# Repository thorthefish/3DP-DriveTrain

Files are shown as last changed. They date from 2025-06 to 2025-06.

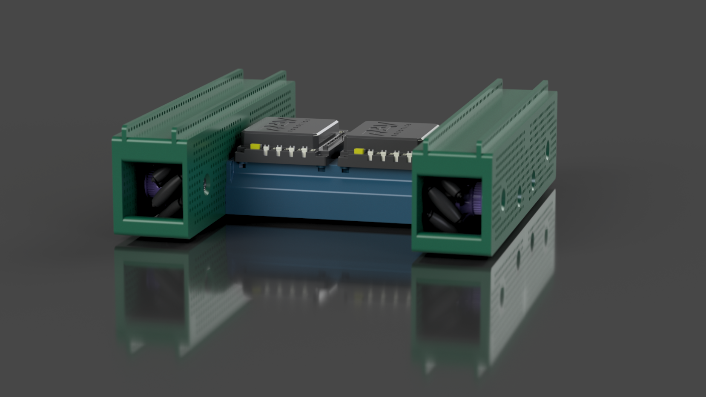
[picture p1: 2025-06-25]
Pictures/render_1.png

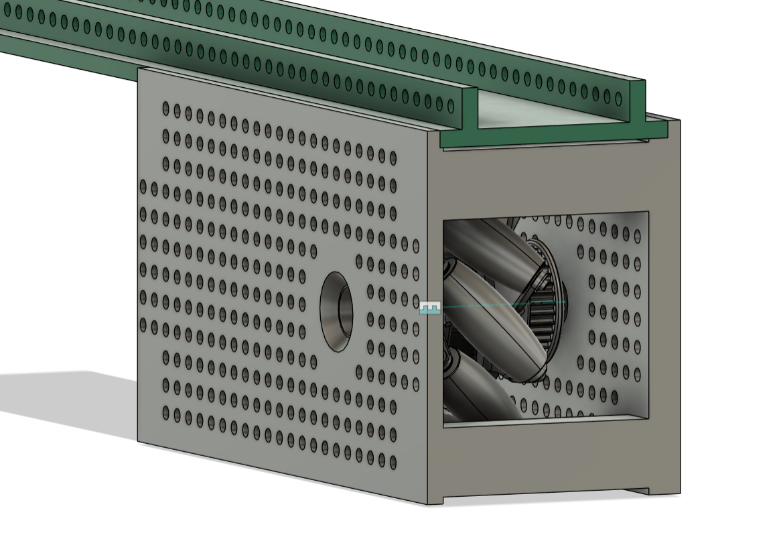
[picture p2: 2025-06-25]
Pictures/Fusion360_dO0HVU8Hnw.png

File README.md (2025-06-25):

# 3D Printed FTC Drivetrain
A Fully 3D Printed FTC Drivetrain

----

render_1

# WHY???

The reason behind this project is my dream for a good, customisable, and strong drivetrain. Whenever it is brought up, it usualy leads to immidiate dismissal, so this is to prove to all teams that a 3D Printed chassis is a good choice for a chassis. This proves that 3D printing is strong enough to compete with aluminum, light enough to compete with carbon fiber, and more versitle than either.

# What

This is A drivetrain using 3d printed parts wherever possible. It is compatable with the gobilda architecture for connecting to most of their standard products (eg. viper slides)

- It can be easily adjusted to almost sny situation, and is incredibly easy to add parts and modules to. 
- works in 3 dimensions, unlike traditional parallel plate designs
- Easy to design around, This is not limited to a single season, it can be addaped to almost any game with a few hours of CAD.
- Mounting, Top rails for any modules immaginable, grids on wass for anything form team markers, odo pods, to linear slides
- Incredibly light, uses around 1kg of filament for an entire chassis

# CAD

Fusion360_uBIizt1Rju

Fusion360_99nrl9oc8i

Fusion360_UiN48u3bqZ

#FEA(AKA. Finite Element Analisis (AKA. Find Weak Points))

This was the most improtant part of this project, it provided the evidence I needed to show that this was a viable option.
The incredible rigidity of PLA is acctualy crucial to this, as other filaments would deform under lesser pressures, so it is the ideal material in this case.

Fusion360_l8kNUF9FA9

Fusion360_3vuXtYZTeW

----
# Assembly

You need to print two instances of the DT_Wheel_Hub files each, they each go on opposite corners, the two files are mirrored copies of the other. Print one instance of the brace, and attach it with 15 mm M4 bolts, the bottoms should be flush and it should go in the direct middle. Refer to cad if needed. The bolts do not need to be in a specific location, just try to get at least 8 points of contact per side.

----
# BOM

|3DP DT|# Needed|# to Purchase|Price /unit|Price Total|Source|
|-|-|-|-|-|-|
||||||
|To Buy| | | | | |
||||||
|Filament 2kg |1 |1 |26 |26 |https://www.amazon.com/ELEGOO-Filament-Dimensional-Accuracy-Cardboard/dp/B0BM7465PB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|
|Timing belts - HTD 3 100T |4 |4 |7 |28 |https://www.gobilda.com/3403-series-3mm-htd-pitch-timing-belt-15mm-width-300mm-pitch-length-100-tooth/ |
|Bearings - 14mm OD 8mm ID Flanged 2pc |2 |2 |4 |8 |https://www.gobilda.com/1611-series-flanged-ball-bearing-8mm-id-x-14mm-od-5mm-thickness-2-pack/ |
|Shafts - 72mm REX |4 |4 |5 |20 |https://www.gobilda.com/2106-series-stainless-steel-rex-shaft-8mm-diameter-72mm-length/ |
|REX Sonic Hubs |4 |4 |8 |32 |https://www.gobilda.com/1309-series-sonic-hub-8mm-rex-bore/ |
||||||
|Alredy Owned | | | | | |
|Hubs |2 |N/A |N/A | | |
|Battery |1 |N/A |N/A | | |
|Odo Pods |2 |N/A |N/A | | |
|Motors |4 |N/A |N/A | | |
|Wiring |Lots |N/A |N/A | | |
|Wheels |4 |N/A |N/A | | |
|M4 Screws |Lots |N/A |N/A | | |
||||||
|Grand Total:| $124 |||

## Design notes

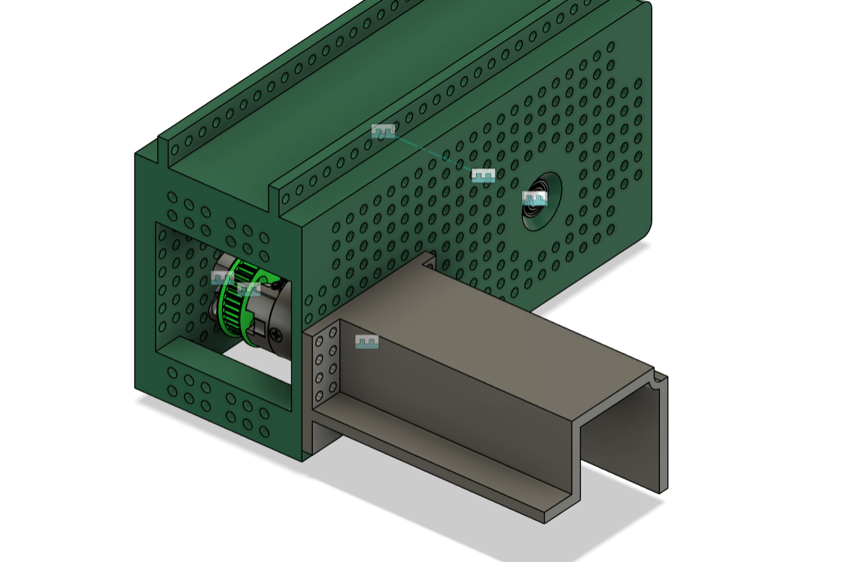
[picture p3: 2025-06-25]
Pictures/Fusion360_UiN48u3bqZ.png

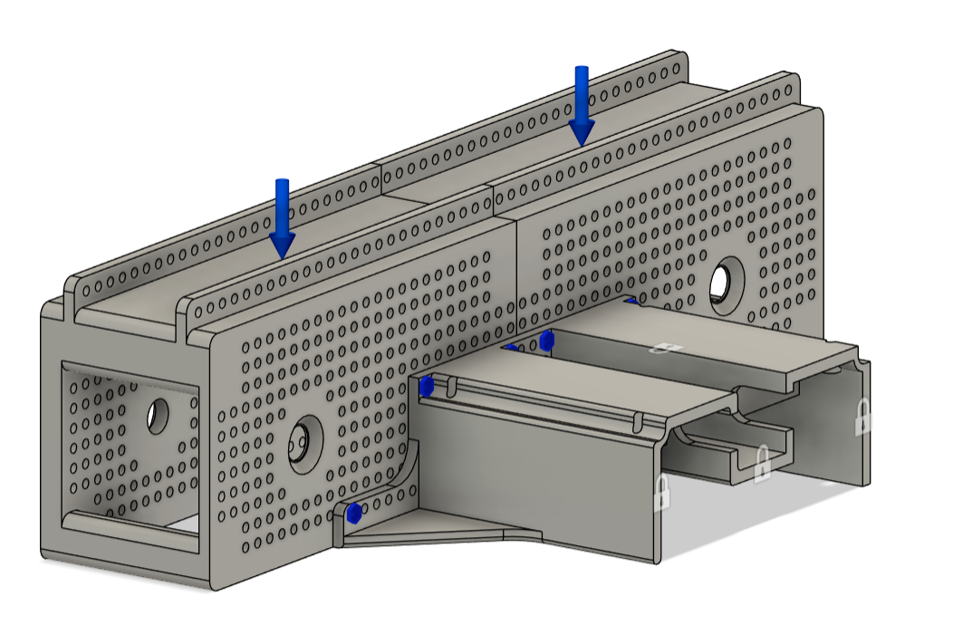
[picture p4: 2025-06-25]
Pictures/Fusion360_K4OMfoFxmH.png

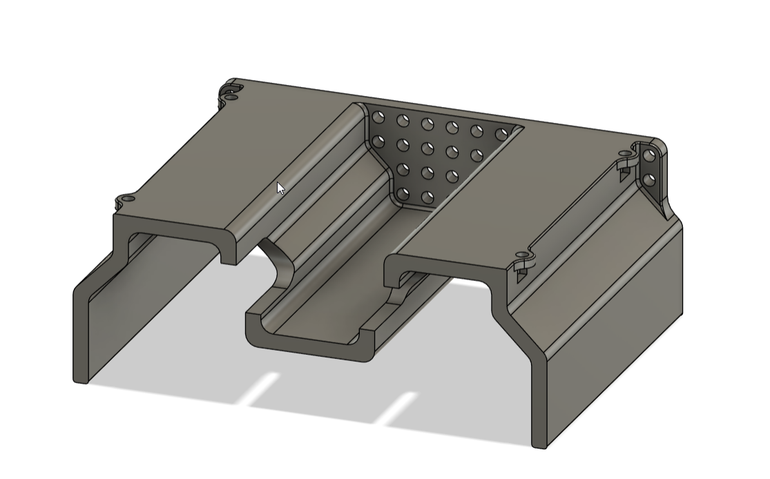
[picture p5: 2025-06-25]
Pictures/Fusion360_h0JIOzbhoG.png

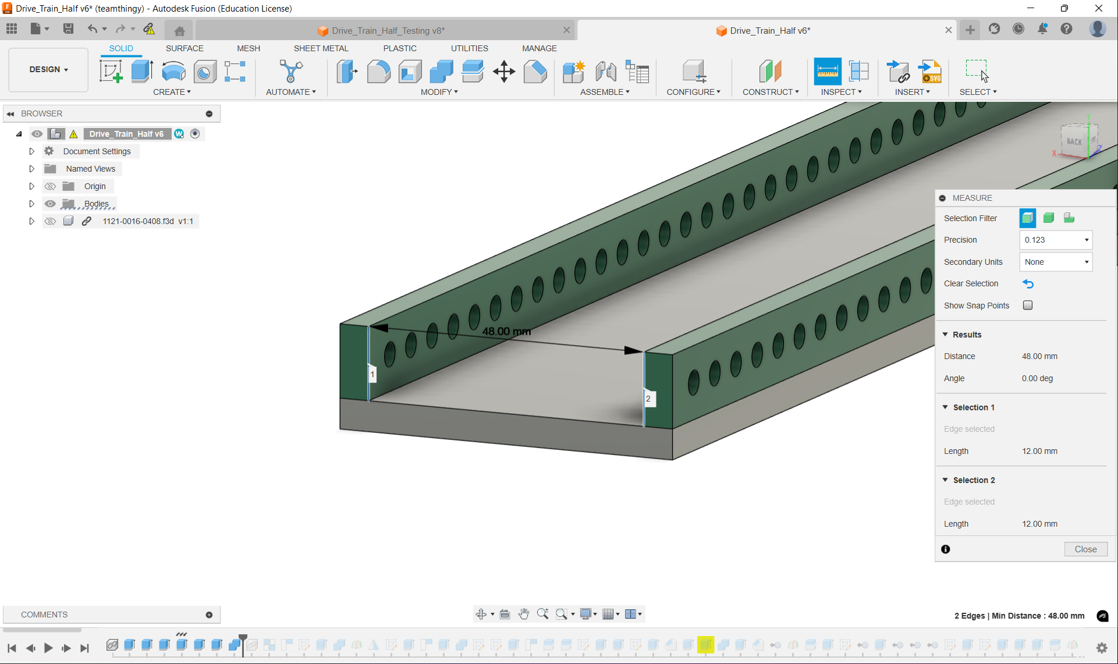
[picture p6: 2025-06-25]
Pictures/Fusion360_yo2hAeYhpV.png

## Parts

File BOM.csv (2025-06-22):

3DP DT | # Needed | # to Purchase | Price /unit | Price Total | Source | Alt
*ALL PRICES ROUNDED UP, BUT SHIPPING NOT FACTORED
To Buy |  |  |  |  |  |  | TOTAL ESTIMATED USD | $114.00 | Amazon:
Filament 2kg | 1 | 1 | 26 | 26 |  |  | Subtotal USD | $0.00 | Gobilda
Timing belts - HTD 3 100T | 4 | 4 | 7 | 28 |  |  | TOTAL w/ 7% TAX USD | $121.98
Bearings - 14mm OD 8mm ID Flanged 2pc | 2 | 2 | 4 | 8 |  |  | Remaining USD | $114.00
Shafts - 72mm REX | 4 | 4 | 5 | 20
REX Sonic Hubs | 4 | 4 | 8 | 32
 |  |  |  | 0
 |  |  |  | 0
Alredy Owned
Hubs | 2 | N/A | N/A
Battery | 1 | N/A | N/A
Odo Pods | 2 | N/A | N/A
Motors | 4 | N/A | N/A
Wiring | Lots | N/A | N/A
Wheels | 4 | N/A | N/A
M4 Screws | Lots | N/A | N/A
 |  | N/A | N/A
 |  | N/A | N/A
 |  | N/A | N/A
 |  | N/A | N/A
 |  | N/A | N/A
 |  | N/A | N/A

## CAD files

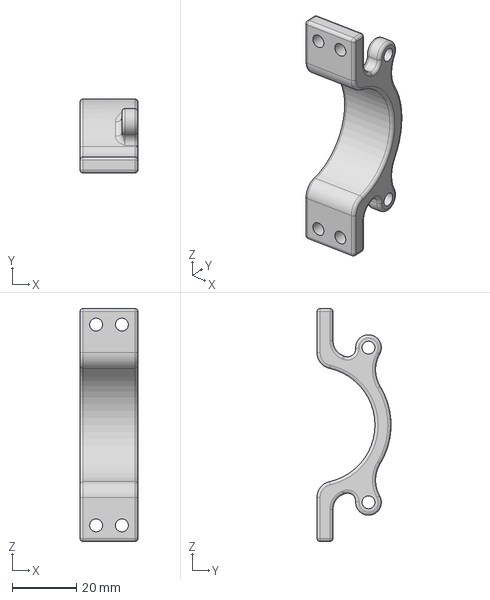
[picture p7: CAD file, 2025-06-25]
CAD/Motor_Clamp_Half.step
18.0 x 23.0 x 72.3 mm

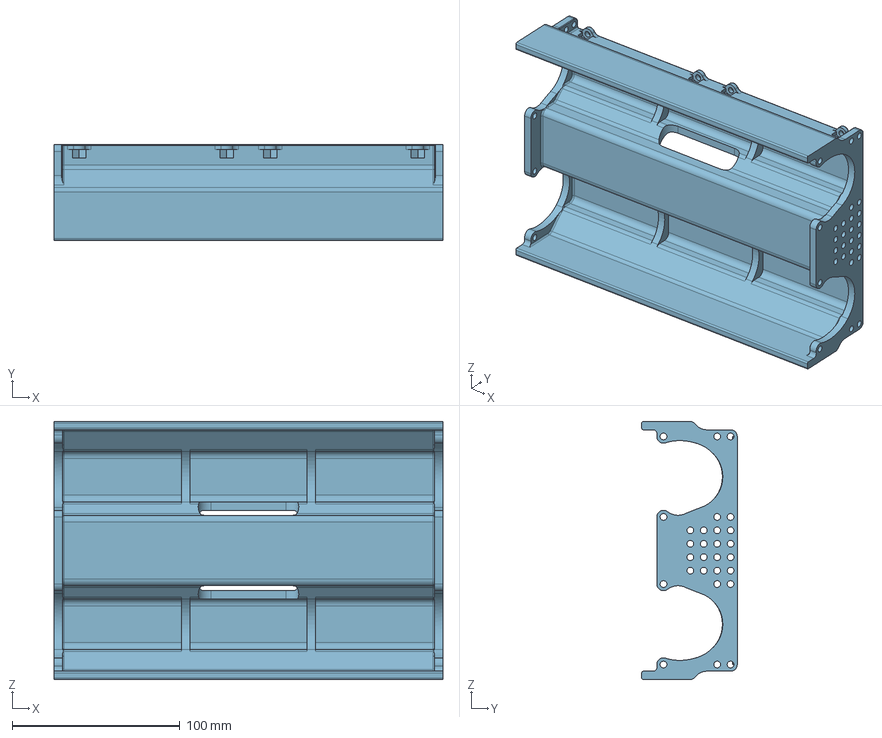
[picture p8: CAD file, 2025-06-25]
CAD/DT_Brace.step
232.0 x 57.0 x 154.0 mm

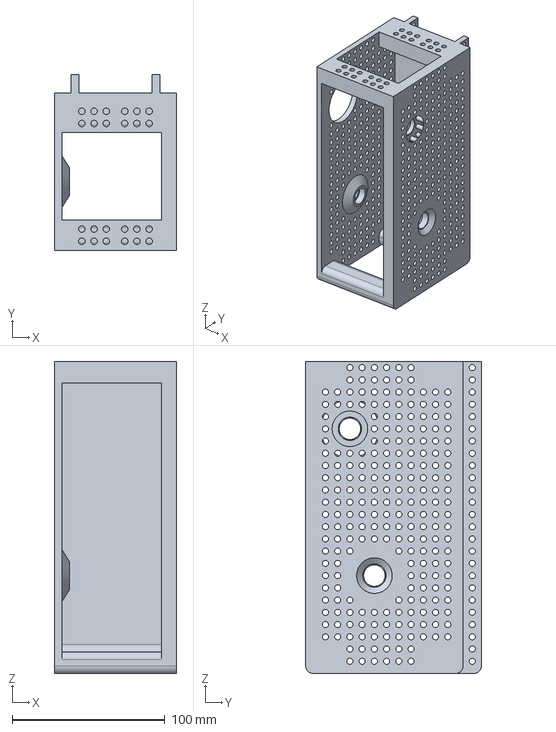
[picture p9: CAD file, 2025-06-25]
CAD/DT_Wheel_Hub_Back.step
80.0 x 115.0 x 204.0 mm

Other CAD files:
CAD/DT_Wheel_Box_Front.step
CAD/DT_Wheel_Hub_Front.stl
CAD/DT_Brace.stl
CAD/DT_Wheel_Hub_Back.stl
CAD/Motor_Clamp_Half.stl

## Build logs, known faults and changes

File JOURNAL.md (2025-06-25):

## All 3D Printed FTC Drivetrain
----
```
Title: 3DP Drivetrain

Author: ryan d

Description: A FTC Drivetrain using as many 3d printed parts to crate the most customizable, durable, and CHEAP as possible

Created: 6-21-2025

Time spent: 25 hours
```
----

# 6-19-2025 - 8 Hours
## Layout

I started with getting the top mounting rails down. These are designed to have a 48mm gap between the two, as to mount any gobilda products that follow that standard. They can also hold any other mounting hardware that we need, as it will be easy to just print mounting hardware

88L7ImE

After that, I went onto the wheel placement, and I just made sure that they had enough ground clearance with a 108mm height for the whole assembly.

Fusion360_DaYXXIthQX

## Modeling

Then, I added the Grid Munting system, all alligned on 8mm grid to work with gobilda parts (What we use for the most part)

Fusion360_X9xPGkcogC

Mounting points to attach the two pods of the drivetrain togeather to form a half. It had to be split in order to fit on one printbed, and simply bolting the two togeather is the most effective way to do so.

Fusion360_Sx9Qb9Y8nO

The part was mirrored  to create the mostly finished pod

Fusion360_dO0HVU8Hnw

---- 

# 6-20-2025 - 6 Hours
## Motors

I got the pulley for the HTD 3 Belt imported, and then alligned it with the best spacing for a 100 tooth belt, and got the motor alligned to find the right place for a mount

Fusion360_YkTrWI9q8y

Next cam a mount for the motor, and with a clamping mount and bearing support on the extririor wall, it will have plenty of support. For now, I am just using 435 motors on a 1:1 but it will be easy enoughh to change that if that is deemed inadaquit.

Fusion360_fJ4oJ7ra5m

The cover for the motors is both a protective mesure, and the main structural brace for the robot. It will be the connection between the two halves of the chassis, eventualy provinding wire management, and hub, odo, and battery mounts.

Fusion360_ghwo6ZCcd7

Fusion360_UiN48u3bqZ

I spent the rest of the time further refining and ended up with this:

Fusion360_99nrl9oc8i

The full assembly so far:

Fusion360_uBIizt1Rju

----
# 6-21-2025 - 4 Hours
## FEA

This is the coolest part by far, its a bunch of simulations and the coolest looking models ever. As a bonus they have some useful info.

I did several simulations in fusion to test if this design could acctualy take the forces it would expirience in competitions, so I decided on doing a first simulation of forces pushing the two halves appart from the top.

----

Setup: 

Fusion360_VxilaGZbVu

Displacement:

Fusion360_l8kNUF9FA9

Stress:

Fusion360_3vuXtYZTeW

----

With less than half a mm from 100 neutons, this is more than satisfactory. for lateral stresses, this drivetrain will be more than capable of withstanding most anything, especialy because plastics, and PLA in particular are incredibly impact resistand. If necisary we could try to print it in TPU, just for that near invulrability

Then the vertical loads:

----

Setup:

Fusion360_K4OMfoFxmH

Displacement:

Fusion360_Ucz5qTIiVf

Stress:

Fusion360_LewLiQoi0W

----

Again, more than enough. This load was 125 N, and with that little deflection, this will be a plenty rigid, and much mor importantly, an incredibly strong chassis.

# 6-22-2025 - 6 hours
## BOM

I spent some time just getting the BOM formmated, and getting all of the parts loaded in, and wow did I underestimate the cost, the preliminary cost was around $200, but after taking off some of the bearings, and estimating what we would have avalable, I got the total down to around $150, but that is still way to expensive, so i decided to try and eliminate the motor clamping mounts first, as they were $40 alone.

## CAD & FEA

I just modeled a basic replacement, that has an extra set of holes to bolt them togeather.

F2KI6HQ9Af

Then I just ran a couple of simulations to eliminate weakpoints, and ended up with very promising results.

----

Setup:

Fusion360_rUoUMmScyy

Displacement:

Fusion360_jduuymUyhZ

Strain:

Fusion360_fNPN24BdQP

----

I also redesigned the motor cover/brace:

Fusion360_h0JIOzbhoG

Started a render on fusion, idk how long imma give it.

#6/25/2025 - 1 hour

##Repo Work

Added a bunch of cad and pictures to the repo. Also finnialy got a good render without having the front blury, just had to crank up the focal legnth of the render, so i just let that go in the background, and let it go for 1 hour exact (cuz even numbers r just happy).

anyway heres the render:

render_1

Might end up playing with the grond effects, but this looks just fine for now.

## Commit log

2025-06-22 Add CAD Files
2025-06-22 Add BOM
    [BOM.csv]
2025-06-25 Individual CAD
    [DT_Brace.step, DT_Brace.stl, DT_Wheel_Box_Front.step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]
2025-06-25 CAD and Pics
    [Motor_Clamp_Half.step, Motor_Clamp_Half.stl]
